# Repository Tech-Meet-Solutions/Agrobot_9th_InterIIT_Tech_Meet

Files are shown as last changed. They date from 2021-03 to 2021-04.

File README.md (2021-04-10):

# Agrobot Design Innovation Challenge
## Rural Technology Action Group - North East (RuTAG-NE)

This repository is a collection of files including simulations, CAD models and documentation created by the IIT Bombay contingent for the Agrobot Design Innovation Challenge by RuTAG-NE for Inter-IIT Tech Meet 9.0 by IIT Guwahati.  

## Abstract  

North-East India has several favorable features for agriculture from fertile land to abundant water resources (high and dependable rainfall). It has a potential to utilize these optimally for agricultural productivity. We propose to design a cost-effective, eco-friendly, and easily operable agricultural robot to convert the incumbent but less effective subsistence farming into efficient mechanized farming by harnessing appropriate niche potentials of marginal mountain land. Our Agrobot deals in particular with effective braking in hilly terrains, transplantation of plants, seed metering, and weed removal, and we do suggest extra features that may supplement the needs of the farmer on an as-needed basis.  

## The Team  

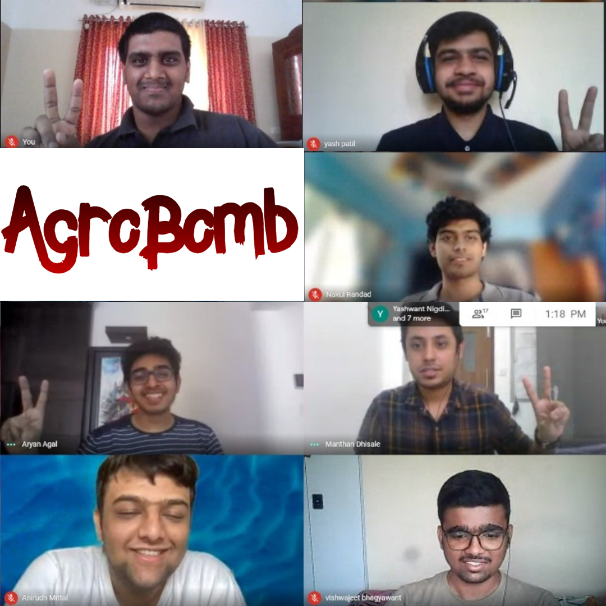
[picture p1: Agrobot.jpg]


But we miss Kaustubh and Jatin in the pic... Anirudh Mittal is the General Secretary - Technical Affairs, IIT Bombay (2020-21), and Aryan Agal and Manthan Dhisale are the Contingent Leaders of the IIT Bombay Contingent, Bombay76, for the 9th Inter-IIT Tech Meet.  

## Team Members

- [Nakul Randad](https://nakulrandad.github.io) *(Team Lead)* 
- [Aaron John Sabu](https://sites.google.com/view/aaronjs/)  
- [Vishwajeet Bhagyawant](https://vishwajeetiitb.github.io/) *(Team Lead)* 
- [Jatin Prashath](https://www.linkedin.com/in/jatin-prasath-399546183/)  
- [Yash Patil](https://www.linkedin.com/in/yash-patil-675863194/)  
- [Kaustubh Patil](https://www.linkedin.com/in/kaustubh-patil-04/)  

### The contingent won Bronze Medal 🥉 in the RuTAG-NE Agrobot Design Innovation Challenge.

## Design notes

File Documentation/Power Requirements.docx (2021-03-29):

Actuator Description | Number of Pieces | Unit Power | Total Power
Locomotion Motor | 4 pieces | 1000 W | 4000 W
High-Power Stepper Motor | 4 pieces | 100 W | 400 W
Stepper Motor (NEMA23) | 1 piece | 9 W | 9 W
300 mm stroke pneumatic cylinder | 1 piece | 50 W | 50 W
50 mm stroke pneumatic cylinder | 2 pieces | 20 W | 40 W
Solenoid valves | 3 pieces | 15 W | 45 W
Servo motor | 1 piece | 7.5 W | 7.5 W
Stepper motor (NEMA23) | 2 pieces | 9 W | 18 W
Gimbal Stepper Motors (NEMA17) | 2 pieces | 15 W | 30 W
Powder gate servo motor | 1 piece | 7.5 W | 7.5 W
DC Motor | 1 piece | 35 W | 35 W

Total Power Requirement = 4000+400+9+50+40+45+7.5+18+30+7.5+35 = 4602 W

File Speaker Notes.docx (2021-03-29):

# Speaker Notes

# (RuTAG) NORTH EAST's AGROBOT DESIGN INNOVATION CHALLENGE

### 2021-03-28

AARON (Backup: NAKUL)

# Slide 01

- Hi everyone. Here’s a quick look at our design for the agrobot.

# Slide 03

- Being modular in design, our robot can carry out tasks such as sapling transplantation, weed removal, and seed metering not just on planes but also in hilly terrains.

# Slide 07

- The agrobot uses a 4-wheel drive with individual steering instead of a differential turning mechanism for more traction and less slippage on loose soil.
- Moreover, the steering motors can align the wheels in a staggered manner for braking.
- The robot features an adjustable chassis to alter wheel separation.

# Slide 13 (Video)

- The proposed bot can sow seeds of irregular sizes at an adjustable rate with uniform penetration into the soil.
- Given the physical characteristics of the seed, we calculate the seed shape index to decide the appropriate rotating disc for the metering mechanism.
- The plastic parts in the mechanism also reduce the possibility of damage to seeds.

# Slide 19 (Video)

- Here are the main features of the transplantation module:
  - Uniform plantation is incorporated, resulting in higher yield.
  - The bot can be refilled directly with a nursery seedling tray in which saplings have been grown.
  - The bot can also plant seedlings according to specified depths as required by the plant.

# Slide 23 (Mechanical vs Chemical, Traditional vs Precision)

- When we think of weeding, we first think of a mechanical weed removal technique.
- But successful mechanical weeding requires the complete uprootal and disposal of weeds, and hence extremely precise and complex mechanisms.
- Chemical weeding, being much faster, is also more scalable in medium-scale and large-scale farms.
- These reasons demand the need for using weedicides.
- We particularly promote precision spraying for increasing the efficiency of spraying and hence decreasing the farming costs.

# Slide 27

- The extra features of the agrobot include the use of renewable power sources, terrain mapping and the identification of water stagnation zones.
- Moreover, a cooperative ownership model can be adopted and custom hiring centres developed for ease of access to the agrobot.

# Q&A

INNOVATIONS

- We have an adjustable chassis and independent steering
- We have developed sowing capability for irregular seeds using controlled metering
- The design implements a full-fledged sapling transplantation mechanism for the given size class of robots
- We have implemented chemical weeding due to the cons of mechanical weed removal. The farmer may also use organic weedicides to reduce the injection of chemicals into the food chain.

DIMENSIONS OF ROBOT

- Dimension: 0.8m x 0.8m x 0.7m
- Weight: 55kg
- Speed: RPM is high. Can reach >2m/s
- Optimum speed considering our use case: 0.5m/s
- Ground clearance: 20 cm
- Battery: 2*22Ah, 22.2V, 2hr endurance
- Steering motor torque: 42 kg-cm

CONTACT OF CROP WITH WEEDICIDE

- This also reduces the contact of the crop with the weedicide, even when the farmer chooses to use inorganic chemicals.

# Speaker Notes

# (RuTAG) NORTH EAST's AGROBOT DESIGN INNOVATION CHALLENGE

### 2021-03-27

NAKUL

A very good afternoon to one and all present here

# Slide 1

Let's start with some food for thought! What if our farmers do not need to carry out farming tasks in scorching sun or some extreme weather? Can't we use our so-called technological advances to help them with these seemingly trivial tasks.

Here we present our concept for The AgroBot to cater their needs.

Firstly let's see the major hurdles in farming related activities.

# Slide 2

Labor shortage, smaller land holdings, inferior farm yield and lower tendency to adopt new mechanisms are few of the many problems that AgroBot can help eliminate.

# Slide 3

With a modular design our robot can carry out tasks like sapling transplantation, weed removal, seed metering not only on planes but in hilly areas as well.

I call upon Yash to dive into the mechanisms in detail.

YASH

# Slide 4

So coming to slippage prevention system

# Slide 5

As our main target was to mechanise agriculture in hilly terrain , our bot has 3 salient features structurally modified wheels

manoeuvring and alignment on these slopes, the

4-wheel drive design with high ground clearance

The wheels consist of rigid-rim, wire-mesh tires that are connected to their axles by spokes. Metal cleats are also mounted on the tire to ensure better traction in the loose soil.

Center of gravity is tried to kept as low as possible

# Slide 6

Components of different

Adjustable rod : Adjust track and wheelbase

High ground clearance and low COG

# Slide 7

2 systems incorporated to avoid slippage

Control system and Mechanical system

4 wheel drive as the soil is loose to avoid slippage and it will give better traction

On high gradient surface the staggered alignment of wheel help in maintaining the position of the bot

NAKUL

# Slide 8

Now coming to the seed metering mechanism, this is an important task as we need to monitor the number of seeds soon at a location without wasting them.

# Slide 9

The design proposed by us can sow seeds of irregular varied sizes at a controllable rate with uniform penetration in the soil.

# Slide 10

The components of the mechanism are shown here. This includes a seed storage box, a continuously rotating disc with slots for seeds, mechanism to put the seeds appropriately in the slots and finally seed sowing pipe.

# Slide 11

Given the dimensions and phy characteristics of the seed we calculate a seed shape index which helps us decide the rotating disc to be used for the metering mechanism.

Of course these discs are easily replaceable.

The plastic parts in the mechanism reduce the chances of damage to the seeds.

# Slide 12

The mechanism as earlier seen in the picture follows this routine.

1) Seeds are first dumped into the hopper and later put into appropriate slots in the rotating disc which fall into delivery pipe

3) and finally the seeds are sown at uniform penetration through a pneumatics actuated delivery pipe.

# Slide 13

Lets watch a quick simulation of the working of mechanism

# Slide 14

With the angular velocity of rotating disc, forward velocity of robot and the state of pneumatics actuated delivery pipe we can control the number of seeds to be sown at what location.

This shows all the boxes for seed metering mechanism are thus checked.

# YASH

# Slide 15

Uniform plantation: equal spacing between plants ...gives higher yield

Refill the bot : Farmer can directly add the sapling trey from nursery into the bot

Plantation to required depth; as every plant requires different depth for growing optimally

# Slide 16

Seedling gripper : Mechanically holds the sapling and drops it into the seedling planter mechanism

The tray is moved through the motors as a conveyer belt

# Slide 17

The next modular accessory is transplantation,

The main features are

Firstly, the uniform plantation - which results in higher yield

Second, you can refill the bot directly with your nursery seedling tray in which you have grown your sampling

And last but not least it will plant the seedling according to the required depth

Coming to the mechanical part

It comprises two mechanisms

1st is seedling gripper & 2nd is a seedling planter

# Slide 18

The mechanism is way simpler,

It contains the gripper which grabs the seedling from the tray and drops it in the planter,

And at the same time another mechanism for moving the tray along the row when the seedling is removed from the hole, and when rows are finished the tray is moved down with the help of another mechanism

AARON

# Slide 20

- As we all know, weeds are a scourge for farmers.
- They reduce crop yield and even poison the soil.
- Weed removal is an essential requirement for any farmer and hence finds its way into our design.

Slide 21

- Our weed removal mechanism features the following characteristics:
  - Organic weedicides that nourish the soil can be loaded into the mechanism.
  - The farmer may spray both liquid and powder in a very precise manner.
  - This mechanism can also be used to sprinkle fertilizers to the plants.
  - And the nozzle of the mechanism is customizable to permit widespread spraying as well as focused spraying.
- Here are some details of our mechanism:
  - The 2-axis gimbal permits spraying throughout the region around the bot.
  - An atomizer is implemented as a very thin tube for spraying liquid weedicide.
  - The junction permits the mixing of solid and liquid with compressed air for precise and focused spraying.
  - An agitator can also be used to maintain smooth flow of powdered weedicide without clogging inside the pipes. We’ll also see more of this later.

Slide 22

- So what’s inside the junction?
  - The upper hole, that’s the smallest hole, is the atomizer through which the liquid weedicide comes out
  - The large middle hole is the input point for compressed air
  - And the hole in the bottom is where the powder comes in.
- For more control, there may also be a gate mechanism for the solid weedicide input and a valve for preventing the flow of compressed air into the liquid weedicide tube.

Slide 23

- The first thought that comes to our minds when we think of weeding is a mechanical weed removal technique. So, why haven’t we suggested that instead of weedicides?
- The complete uprootal, segregation, and disposal of weed are required for successful mechanical weed removal.
- This calls for an extremely precise mechanical arm mechanism that would be complex to implement and would put a dent in the wallet of the farmer. It would also be difficult to maintain in the rough conditions of a farm.
- Moreover, mechanical weed removal may even cause damage to crop roots.
- Finally, mechanical weeding is much slower in comparison to chemical weeding, which makes the latter much more scalable in medium-scale and large-scale farms.
- These reasons demand the need for using weedicides.
- But why not traditional weed removal? Why specifically use precision spraying?
- In terms of weedicide volume, precision spraying is 95% more efficient than indiscriminately spraying weedicides since it sprays only in areas that are detected to contain weed.
- While this saves a lot of weedicide and reduces costs for the farmer, it also puts smaller amounts of chemicals in the food chain even with inorganic weedicides, hence improving the quality of the crop.
- Finally, our weed removal mechanism may use computer vision to detect the location of weeds to prevent indiscriminate weeding which may lead to the removal of crops as well.

Slide 24

- The agitator is a basic mechanism that causes vibrations on the pipes.
- The mechanism works due to the unbalanced force that arises due to the unbalanced mass that is the semi-circular mass that is rotated using the DC motor.
- The agitator is placed midway between the gimbal mechanism and powder tank for optimal performance.

# Slide 25

AARON: So, what’s more? Let’s hear from Kaustubh and Nakul.

KAUSTUBH: Title

# Slide 26

Architecture: The DC battery powers the microcontroller which provides outputs to the motor driver and based on the inputs from the sensors. A solar module can be integrated for recharging the batteries.

# Slide 27

Extra features are

-> Renewable source of power: Hilly regions have high solar irradiation and a 200W solar panel mounted on the roof of the robot is enough to charge two batteries.
Which is utilization of Solar irradiation

-> Gyroscope ground level alert: Using the gyroscope of a smartphone integrated with a bot, the bot alerts farmers where water stagnation can occur .
Which can map the terrain and help identify water stagnation zones with soil moisture sensors

-> All of this can be integrated into a smartphone application for ease of use.

Smartphone integration: Once a farmer connects his smartphone, the bot becomes aware of farm layout, crop type and farm activities to be carried from data in the smartphone. The ambient light sensor , gravity sensor , gyroscope, compass, camera, flash from a smartphone are available for bot to use.

3D printable parts: Several parts of the mechanism plastic made to prevent damage to seeds and saplings and can be modified as per required customisation.

-> Disease assessment on crops and light traps : The light trap mounted on the bot traps insects as it moves through the farm at night. The continuous surveillance using a smartphone camera and a computer vision algorithm keep track of yellowing and rolling of leaves and alert farmers with photos and crop location. Manual steering option: A handlebar at the back of bot gives full steering control with motor locomotion

# Slide 28

Cost issues are answered by implementing cooperative ownership model and custom hiring approach

Energy issues are answered by using renewable energy power.

Innovations can help reducing fixed and variable costs.

# Slide 29

The role of Agrobot in the rural sustainability triangle is explained in terms of economic, socio-cultural and environmental aspects.

Socio-cultural

Rural Social Condition: Due to migration of men to cities, women have to lead farm activities. The mahila mandals, self -help groups (SHGs) in several hilly states have the potential for women in the development of cooperative ownership model and custom hiring centres in hilly areas.

Food Quality:Low use of agro-chemicals indicates considerable potential for ‘organic’ agriculture.

Farmer Safety: high risk of work-related injuries, lung disease, noise-induced hearing loss, skin diseases, as well as certain cancers related to chemical use and prolonged sun exposure

Youth skills: micro enterprises development

Economic

Farmer Income: labour decrease, seed and other input cost,

Sustainable food products: diversify into more lucrative high value crops.

Food supply: subsistence farming into viable farming

ENVIRONMENT:

Soil/ water : New technologies prevent land loss to erosion, water pollution and enhances carbon sequestration.

Biodiversity: Local species of food products (species, fruits, vegetables_ are conserved.

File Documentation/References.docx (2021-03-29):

# References

1. Potential Bioherbicides: Indian Perspectives | SpringerLink (https://link.springer.com/chapter/10.1007/978-81-322-1683-4_15)
2. Distinguish between selective and non-selective herbicides and give an example of each. | Forage Information System | Oregon State University (https://forages.oregonstate.edu/nfgc/eo/onlineforagecurriculum/instructormaterials/availabletopics/weeds/herbicides)
3. Mechanical Weed Control - ScienceDirect (https://www.sciencedirect.com/science/article/pii/B9780128098813000085)
4. Bio-herbicides For Sustainable And Eco-friendly Weed Control: A Review. (journalijar.com) (http://www.journalijar.com/article/26030/bio-herbicides-for-sustainable-and-eco-friendly-weed-control:-a-review/)
5. Limitations of Existing Weed Control Practices Necessitate Development of Alternative Techniques Based on Biological Approaches - ScienceDirect (https://www.sciencedirect.com/science/article/pii/S0065211317300858)
6. Farming Bot: Precision Agriculture System in Limited Land Based On Computer Numerical Control (CNC) (https://iopscience.iop.org/article/10.1088/1755-1315/411/1/012059/pdf)
7. Different Types of Agricultural Robots | RIA Robotics Blog (https://www.robotics.org/blog-article.cfm/Robotics-in-Agriculture-Types-and-Applications/74)
8. Highlights of Himalyan farming book (https://docs.google.com/document/d/1mqfsVbrNtr3RH_c4kIhuxth0uB1VbZMfozKEREzDgDA/edit?usp=sharing)
9. Rowbot (https://rowbot.com)
10. About – Harvest Croo (https://harvestcroo.com/about/)
11. CAD
  a. Motors: https://grabcad.com/library/1020zxf-36v-500w-dc-motor-1
  b. Seedling: https://grabcad.com/library/seed-starter-tray-insert-1
12. Products
  a. Motors: https://robu.in/product/my1020-48v-1000w-electric-go-kart-brushed-dc-motor-with-foot/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

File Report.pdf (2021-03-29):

# Ag r o B o t De s i g n I n n o v a ti o n C h a l l e n g e

## INTER I IT TECH MEET '21

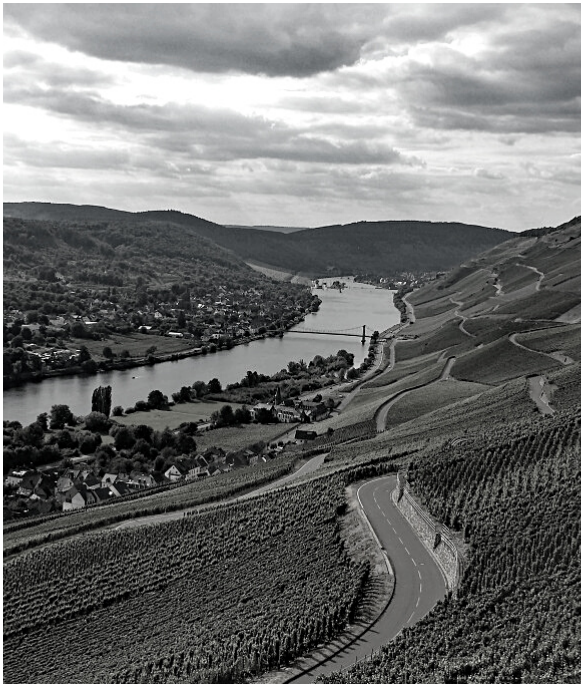
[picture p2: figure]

## Introduction to Solutions

### Literature review and survey

The North-Eastern regions of India have several comparative features like fertile land, abundant water resources, high and dependable rainfall (annual rainfall about 2000 mm), and an agriculture-friendly climate. Yet, it has failed to convert its strengths optimally into growth opportunities in agricultural productivity (Barah, 2006).
We conducted an online survey and telephonic interview to understand the hill conditions, resources available, and people’s socio-cultural setting. The analysis of responses from 28 respondents about farm activities that require mechanization is as follows:

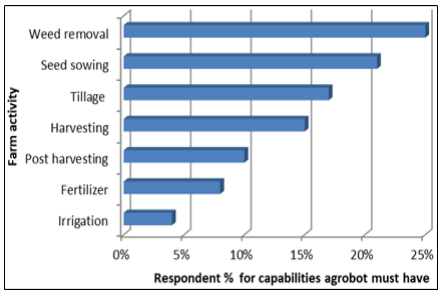
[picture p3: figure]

Fig.1: Survey on AgroBot capabilities

We realized that a major portion of the land in this region has a slope of more than 15°, undulating topography, inaccessible terrain, fragility in moisture stress, and also poor soil conditions. Moreover, socio-economic constraints exist, such as small holdings, poor productivity, production management, labour shortages, poor marketing, and lack of entrepreneurship. The objective was to design a cost-effective, eco-friendly, easily operable AgroBot to convert non-viable subsistence farming into viable farming through harnessing appropriate niche potentials of marginal mountain land.

### Mechanized farming in hilly terrain

Rationale for mechanism
Hilly farming terrains in the North-Eastern regions of India have slope gradients ranging from 2° to 27° (Prokop & Poreba, 2012). The accuracy of position calculated through odometry is affected by slippage between the ground and the wheel or track. When travelling on a loose slope, the localization accuracy of the odometry decreases remarkably due to slippage. To improve its accuracy in such environments, terra-mechanics focuses on estimating the interaction between a vehicle and the ground with visual odometry.

Manoeuvring and alignment on these slopes

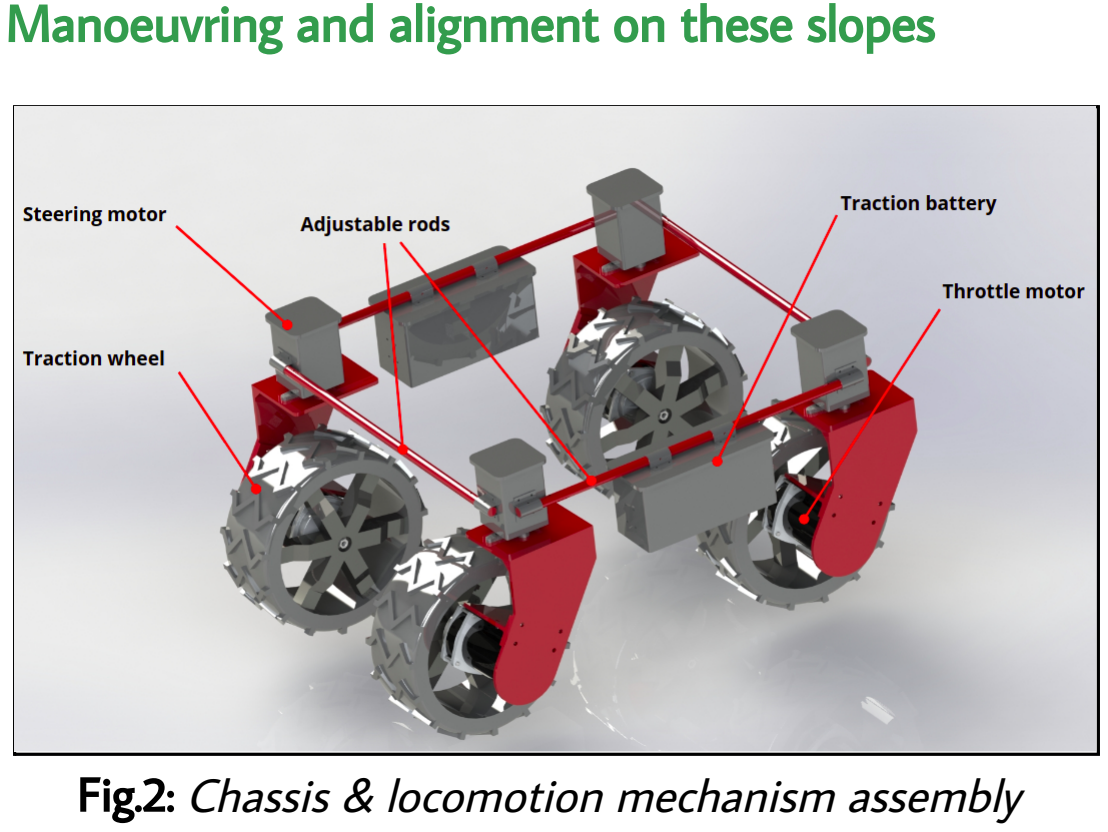
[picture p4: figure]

Fig.2: Chassis & locomotion mechanism assembly

Along with introducing a slip model to the kinematics (control), we also have mechanically modified wheels. A differential turning mechanism is not a preferred way for steering in these environments of low wheel traction. For manoeuvring and alignment on these slopes, the 4-wheel drive design of our robot coupled with each wheel’s independent steering ability serves the purpose. With these capabilities, the vehicle wheels can be aligned in a staggered fashion (see Fig.2) to reduce slippage drastically. The low centre of gravity was aimed to get a stable design that includes mounting battery pods (high-density components) as low as possible.

### A metering mechanism for irregular seeds

Rationale for mechanism
Delays in planting due to labour shortages and rain cause the rotting of rhizomes. Mechanized planting can help overcome labour shortages, improve operational timeliness, and reduce cost, drudgery, and yield losses. The seed rhizome’s shape is irregular and could not be correlated to any standard shape. However, the variability in shape is expressed as ‘Shape Index’ (I

s). The
shape index of the seed rhizome is calculated by the following expression (ISO, 1983):

I

s = [L

2
/ (W · T)] · 100
where L, W, and T (all in mm) are the length, width, and thickness of the seed respectively. Metering mechanisms with three interchangeable disks with cell sizes of diameter 80mm, 30mm, and 10 mm are provided to accommodate different seed sizes. To get the dimension of the seed metering mechanism, the mean length, width, thickness, weight, and shape of seed rhizome along with the standard deviation and coefficient of variation were measured for over 30 rhizome seeds with

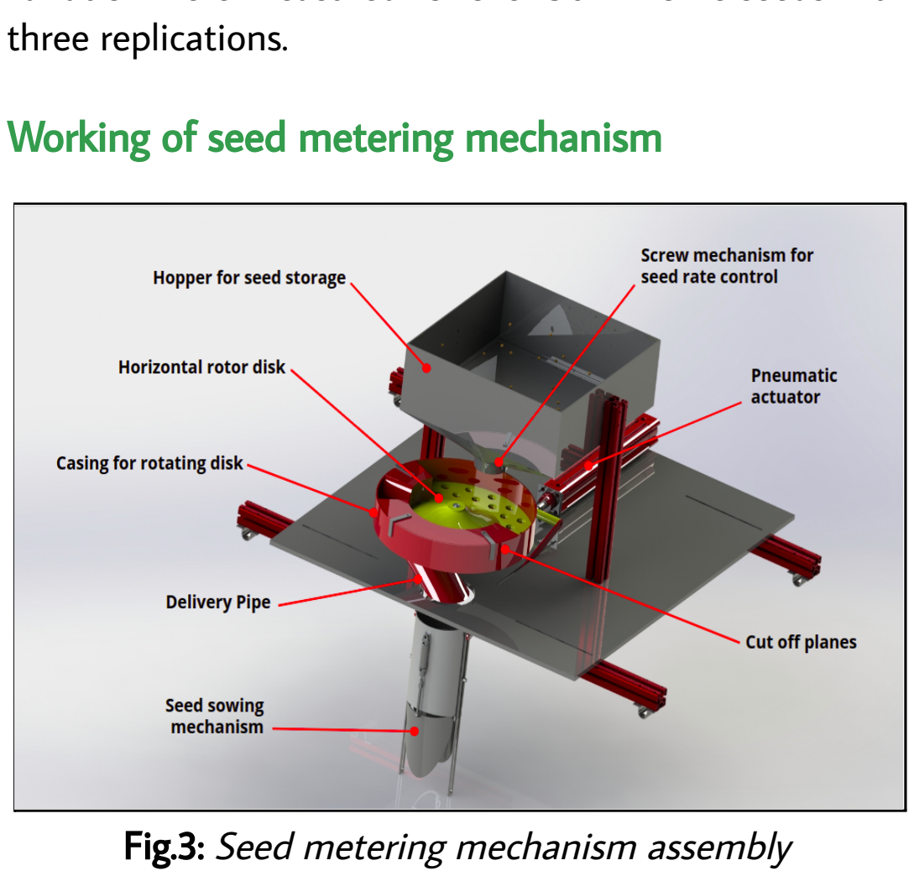
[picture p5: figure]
three replications.; Working of seed metering mechanism; Fig.3: Seed metering mechanism assembly

Seeds are dumped in the hopper from the top. At the bottom of the hopper, a screw adjustment mechanism controls seed rate falling on the horizontal disk rotor. Cut-off plates over the disk ensure that a specified seed amount fills each cell. As each cell approaches the bottom chute in the casing, the seed rhizomes drop in the delivery tube. Calibration of the seed metering mechanism (rpm of the horizontal disc) is calculated based on bot forward speed, seedling spacing, no. of cells, and disc radius. The rotor disk rotation speed ensures seed dropping at the correct spacing between plant to plant. The delivery tube drops seeds in pits created by flap-type planters at required soil penetration. Two flappers at the back of the AgroBot cover the seed with soil and compact the soil around it to enhance germination and emergence. Horizontal disc cell type, the metering mechanism has high cell fill accuracy from past testing and is reliable.

### Transplantation mechanism

Rationale for mechanism
Rhizomes seeds are stored in soil pits in a dry and shaded place between cropping seasons. In this method, around 25-30% of rhizomes rot in the pit itself, and about 10-15% of rhizomes sprout in the hole and are rendered useless for sowing. Transplantation can prevent these losses.
Working of Transplantation mechanism
The transplantation mechanism is inspired by flap-type planters. We have automated a flap-type planter using three pneumatic cylinders, a cylinder for pushing the flaps/blades into the ground, and another two cylinders to open and close the flaps.

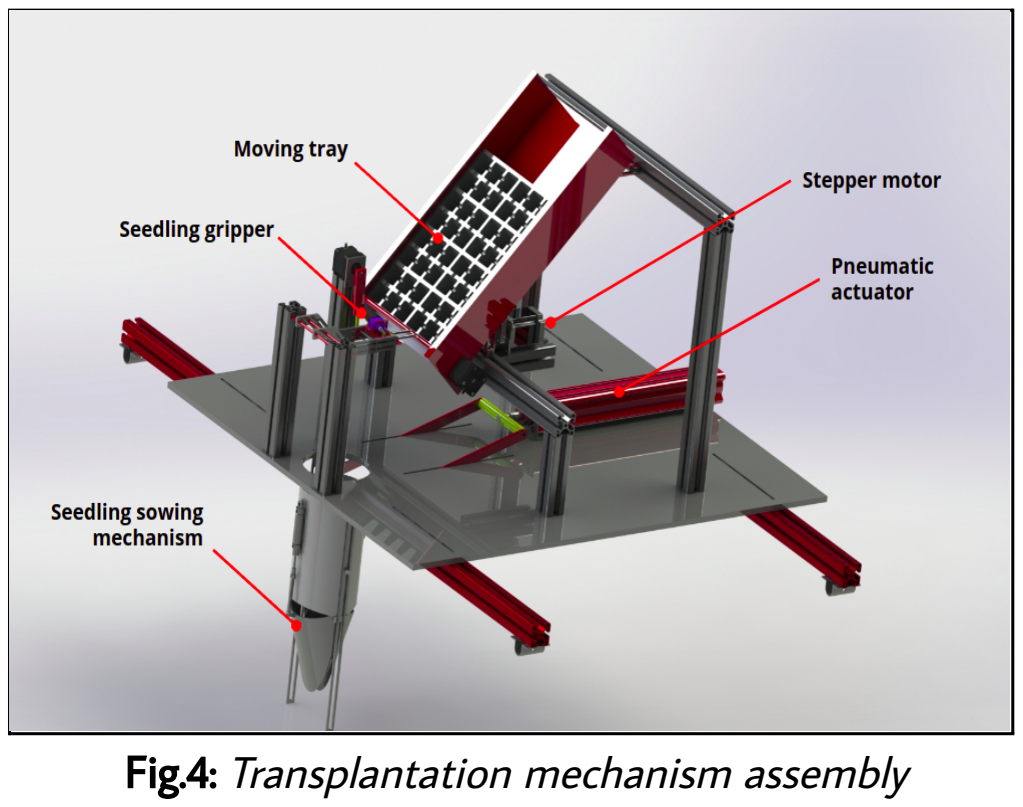
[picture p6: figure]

Fig.4: Transplantation mechanism assembly

The conveyor mechanism is implemented for the automatic supply of saplings to the planter. We have used a tray that will work like a conveyor belt and contain saplings for plantation. The tray will be mounted on a system with 2 DoFs, due to which the tray will be able to move in the azimuthal plane. A gripping / clipping mechanism is also added to drop saplings into the planter. Three motors are being used; 1 servo (for gripping mechanism) and 2 NEMA 23 motors for operating the conveyor tray.

### Weed removal mechanism

Rationale for mechanism
There are two options available for weed removal: mechanical and chemical. We have opted for organic herbicides weed removal for the following reasons: Mechanical weed removal requires the complete uprootal of weeds and their disposition away from the field. If this is not achieved, they will grow back in no time, making the process ineffective. The mechanical weed removal process can trigger soil erosion on steep slopes. Studies on steep slopes have indicated the soil loss of order 40.9 tonnes/ha.

Weeds grown within crop rows and closer to crop plants escape the mechanical remover and can also damage roots. Weeds grown within crop rows incur much higher losses. Furthermore, weed removal products with biological control agents (BCAs) act as sources of nutrition for the soil. They help provide agriculture with effective tools for abundant crop production while minimizing impacts on health and the environment.

Working with herbicide and powder application

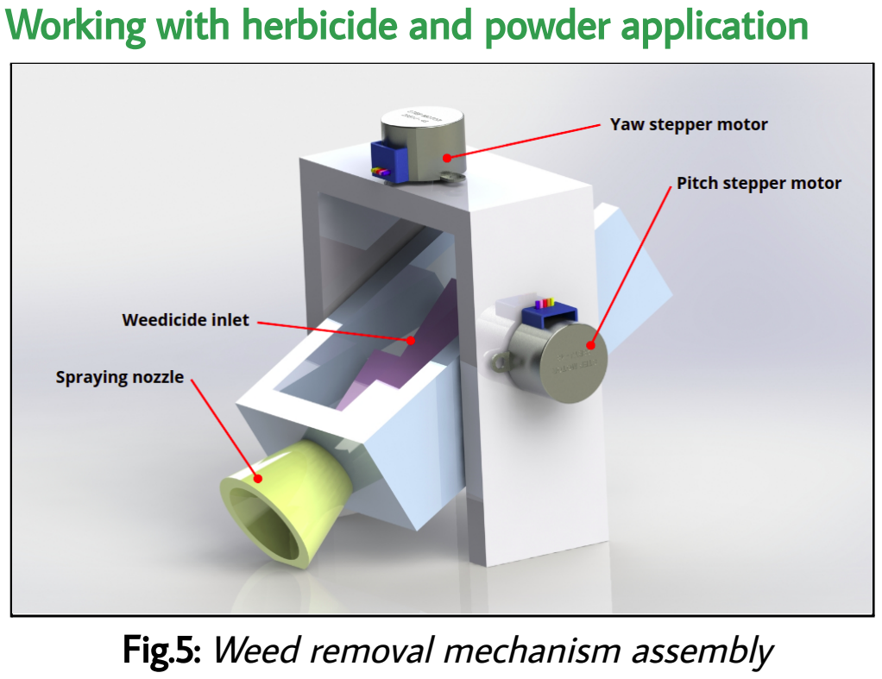
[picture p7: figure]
Fig.5: Weed removal mechanism assembly

Insect-pest control through ITK (Indigenous Technical Knowledge) involves the sprinkling of ash and powdered farmyard manure (FYM). The proposed mechanism can spray both liquid and powdered products. Both mechanisms are operated by spraying air at high pressure through a specially designed nozzle where the air mixes with liquid or powder and then exits via a nozzle. A 2-axis gimbal controls the direction of the nozzle. This allows us to control the region where the product is sprayed and increase the efficiency of spraying the organic product by reducing its wastage. The proposed mechanism can also be used for spraying fertilizers and other kinds of additives.

## Model details

### Mechanical assembly

The robot has a 4-wheel drive design which helps in generating greater torque for the movement. The wheels consist of rigid-rim, wire-mesh tires that are connected to their axles by spokes. Metal cleats are also mounted on the tire to ensure better traction in the loose soil. The seed metering mechanism, transplanting mechanism and weed removal mechanism have a rectangular platform. The platform is bolted to the base frame and the mechanism gets easily integrated. The base rod mounting points are changeable which gives the user freedom to vary the distances between wheels as per the crop/terrain requirement.

### Electronics

IMU (Inertial Measurement Unit): This sensor can help with getting the acceleration and orientation of the AgroBot. The acceleration can be used to calculate velocity and distance travelled. Orientation can further be used to map the terrain and formulate better routes for later runs. The farmer may subsequently utilize this data to plan cropping patterns.
Smartphone Camera: It is used to identify weeds, monitor surroundings, help with navigation and provide visual feedback to the remote user.
Soil moisture & temperature sensor: It is used to measure the volumetric water content of the soil. This helps to plan the farming activities better with proper data collection for each event.
Sensor Positioning: The sensors are attached to the robot’s frame with sturdy mounts, which helps avoid possible damages to the sensor. These mounts are modular, which enables the user to remove and incorporate a sensor into the robot.

### Architecture

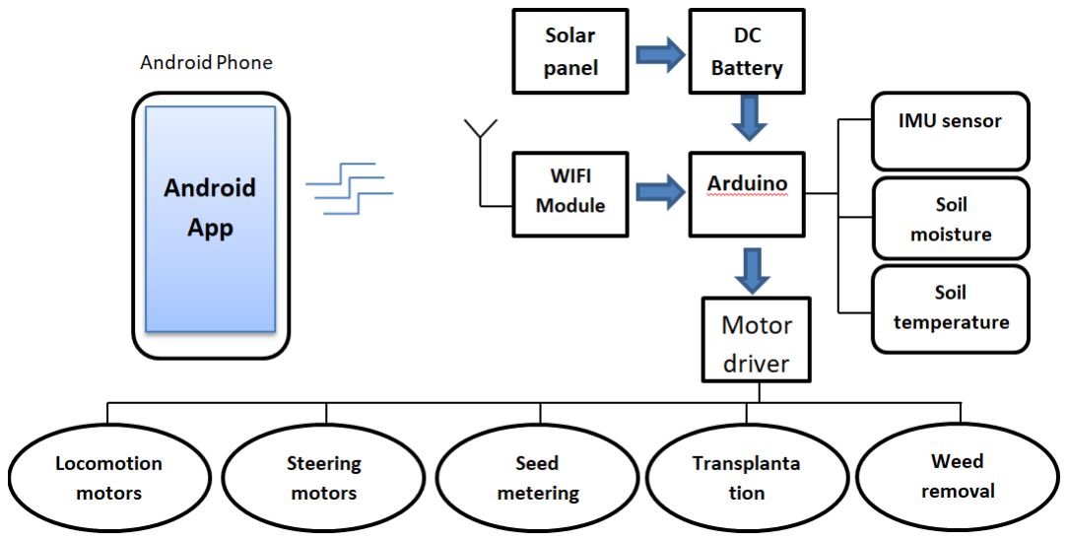
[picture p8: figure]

Fig.6: Block diagram of Agrobot

## Hardware Components & Cost Analysis

Cost for mechanized farming in hilly terrain
Sr. no. | Main component | Sub-components | Cost/pc | Qty
1 | Wire mesh tyres (with extrusions) | Rim | 1200 Rs | 4 pieces
2 | Locomotion Motor (1000 Watts): Throttle* | Fitting and wiring | 5000 Rs | 4 pieces
3 | Stepper Motor (NEMA34) 100 Watts, 42kg-cm: Steering (Link)* | Fitting and wiring | 3000 Rs | 4 pieces
4 | Batteries (22000mAh; 22.2 V) - 1 hr endurance | LiPo type | 11000 Rs | 2 pieces
5 | Solar Panel (200 W, 24 V) - optional | Controller | 5000 Rs | 1 piece

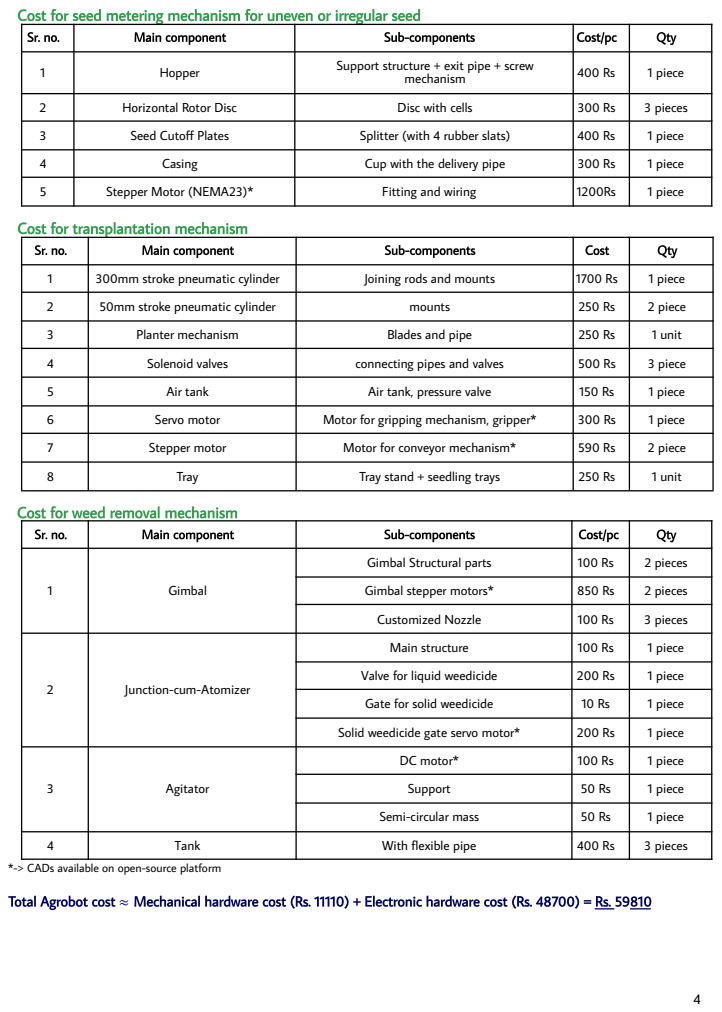
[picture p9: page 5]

Cost for seed metering mechanism for uneven or irregular seed

Sr. no. | Main component | Sub-components | Cost/pc | Qty
1 | Hopper | Support structure + exit pipe + screw mechanism | 400 Rs | 1 piece

2 | Horizontal Rotor Disc | Disc with cells | 300 Rs | 3 pieces
3 | Seed Cutoff Plates | Splitter (with 4 rubber slats) | 400 Rs | 1 piece
4 | Casing | Cup with the delivery pipe | 300 Rs | 1 piece
5 | Stepper Motor (NEMA23)* | Fitting and wiring | 1200Rs | 1 piece

Cost for transplantation mechanism

Sr. no. | Main component | Sub-components | Cost | Qty
1 | 300mm stroke pneumatic cylinder | Joining rods and mounts | 1700 Rs | 1 piece
2 | 50mm stroke pneumatic cylinder | mounts | 250 Rs | 2 piece
3 | Planter mechanism | Blades and pipe | 250 Rs | 1 unit
4 | Solenoid valves | connecting pipes and valves | 500 Rs | 3 piece
5 | Air tank | Air tank, pressure valve | 150 Rs | 1 piece
6 | Servo motor | Motor for gripping mechanism, gripper* | 300 Rs | 1 piece
7 | Stepper motor | Motor for conveyor mechanism* | 590 Rs | 2 piece
8 | Tray | Tray stand + seedling trays | 250 Rs | 1 unit

Cost for weed removal mechanism

1 | Gimbal | Gimbal Structural parts | 100 Rs | 2 pieces

Gimbal stepper motors* | 850 Rs | 2 pieces
Customized Nozzle | 100 Rs | 3 pieces

2 | Junction-cum-Atomizer | Main structure | 100 Rs | 1 piece

Valve for liquid weedicide | 200 Rs | 1 piece
Gate for solid weedicide | 10 Rs | 1 piece
Solid weedicide gate servo motor* | 200 Rs | 1 piece

3 | Agitator | DC motor* | 100 Rs | 1 piece

Support | 50 Rs | 1 piece
Semi-circular mass | 50 Rs | 1 piece

4 | Tank | With flexible pipe | 400 Rs | 3 pieces

*-> CADs available on open-source platform
Total Agrobot cost ≈ Mechanical hardware cost (Rs. 11110) + Electronic hardware cost (Rs. 48700) = Rs. 59810

## Maintenance

Transplantation mechanism
The planter mechanism has a low cost and is easy to repair. Connecting rods can be easily replaced with any metal rod (even cycle spokes temporarily). The only major components that need regular oiling and cleaning are the pneumatic cylinders and their solenoid valves. The solenoid valves may be covered with insulation to function in the rain (there are no other electrical parts). Seed metering mechanism
The seed metering device is easily detachable. It must be cleaned and oiled regularly to ensure its durability. The gap between the disk rotor and casing must be checked for any particle stuck.
Mechanised farming in hilly terrain
The wheels and base are robust and only the motors need regular oiling. The ground clearance is ~ 20 cm which reduces chances of damage to the components. Weed removal mechanism
The mechanism has very few moving parts and hence is durable. The gimbal that controls the nozzle requires maintenance but it is easily replaceable. The agitator attached to the powder carrying pipe is also replaceable by plugging although it is a moving part.

## Extra features

Renewable source of power: Hilly regions have high solar irradiation and a 200W solar panel mounted on the roof of the robot is enough to charge two batteries. Gyroscope ground level alert: Using the gyroscope of a smartphone integrated with a bot, the bot alerts farmers where water stagnation can occur.
Smartphone integration: Once a farmer connects his smartphone, the bot becomes aware of farm layout, crop type and farm activities to be carried from data in the smartphone. The ambient light sensor, gravity sensor, gyroscope, compass, camera, flash from a smartphone are available for bot to use.

3D printable parts: Several parts of the mechanism plastic made to prevent damage to seeds and saplings and can be modified as per required customisation. Disease assessment on crops and light traps : The light trap mounted on the bot traps insects as it moves through the farm at night. The continuous surveillance using a smartphone camera and a computer vision algorithm keep track of yellowing and rolling of leaves and alert farmers with photos and crop location.
Manual steering option: A handlebar at the back of bot gives full steering control with motor locomotion. Humidity and temperature sensors on bot: Regional databases of environmental conditions throughout a geographical location can be sampled by a group of bots.

## Scalability and realisation

Co-operative ownership model and custom hiring to make it scalable for small landowners
The AgriBots will be hired from custom hiring centres and farmers integrate their smartphone with the bot. Employment is generated as bots in custom hiring centers will require maintenance and technological interventions. The significant trend witnessed by the northeastern states in recent times is the change in demographic patterns i.e increased male out migration. This has led to increasing farming-related workload for women. The mahila mandals, self-help groups (SHGs) in several hilly states have the potential for women in the development of these centres in hilly areas.
Value addition for small and marginalised farmers In hilly areas, low use of agrochemicals indicates considerable potential for ‘organic’ agriculture and the AgroBot assists in the same to increase crop intensity. As drudgery reduces, farmers can devote time to microenterprise development like “farming for tourism”. With the use of AgroBots as farmers get accustomed to use of technology they can access market information and move to lucrative high-value crops from local farm produce.

## References

- Barah, B. C. (2006). Agricultural Development in North-East India Challenges and Opportunities.
- International Organisation for Standardization (ISO). (1983). Agricultural Machinery Handbook, No. 13, ISO code No. 5691 (1981), pp. 387-389.
- Prokop, P., & Poręba, G. J. (2012). Soil erosion associated with an upland farming system under population pressure in Northeast India. Land Degradation & Development, 23(4), 310-321.

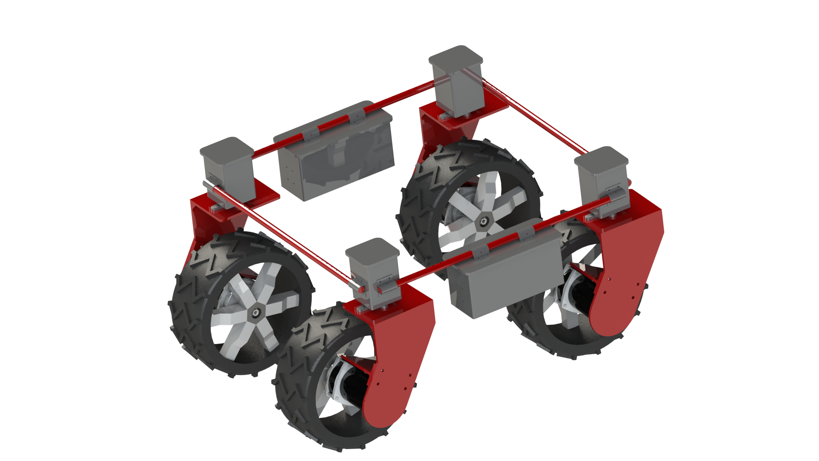
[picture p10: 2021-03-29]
Images/bot_chassis.png

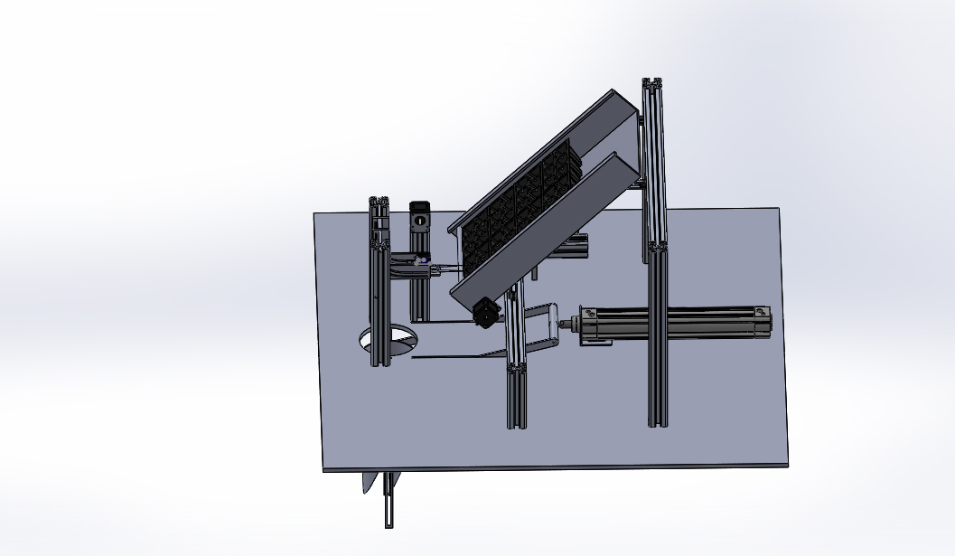
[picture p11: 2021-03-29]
CAD Files/Development/Transplantation/images/final1.JPG

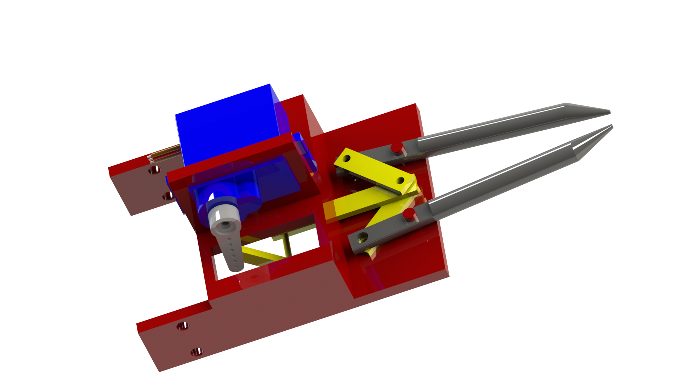
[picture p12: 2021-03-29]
Images/seedling_grabber.png

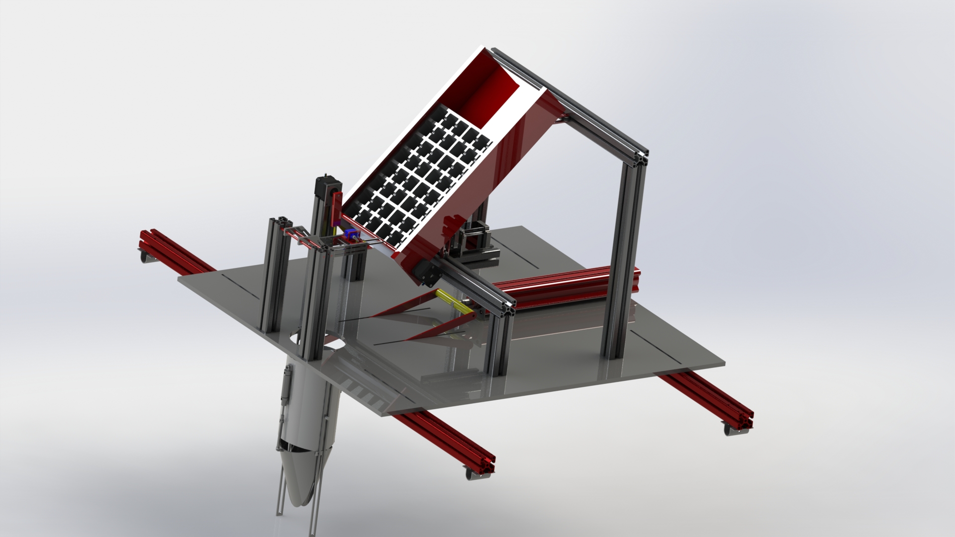
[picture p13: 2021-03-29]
CAD Files/Development/Transplantation/images/transplantation1.JPG

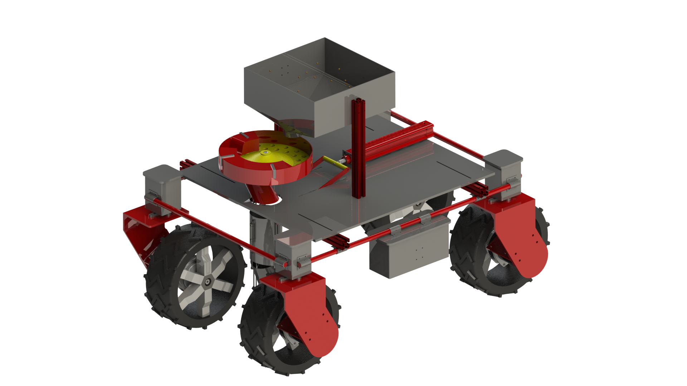
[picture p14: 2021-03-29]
Images/seed_metering_mechanism_bot2.png

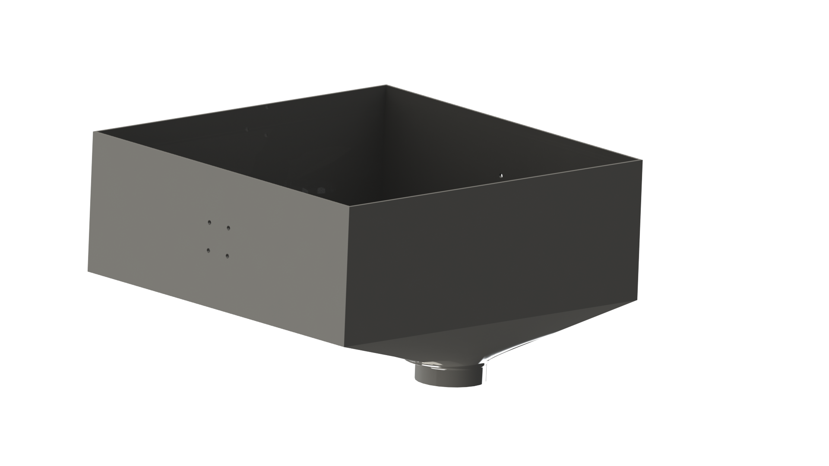
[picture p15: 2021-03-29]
Images/seed_metering_mechanism_seed_holder.png

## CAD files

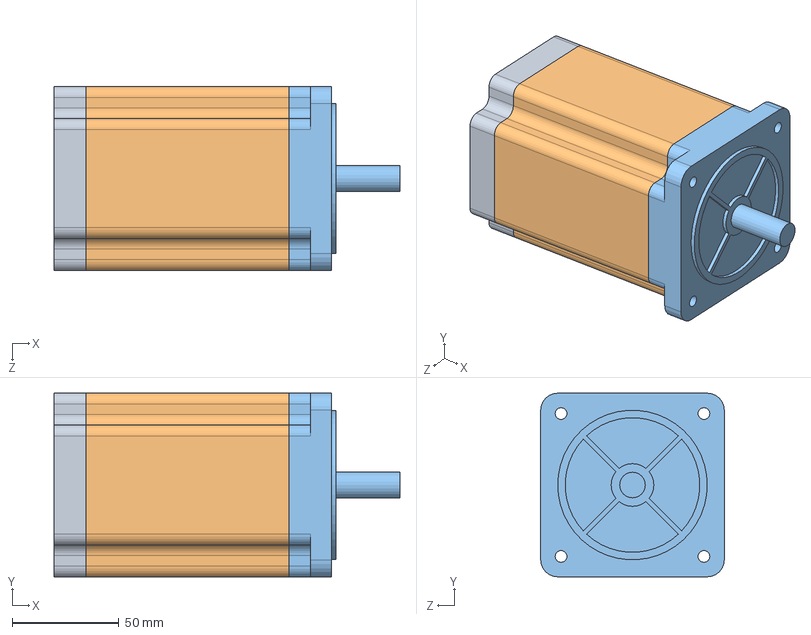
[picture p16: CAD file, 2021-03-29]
CAD Files/Development/Base/Motor/nema-34-step-motor-85kg-stepper-86-130-1.snapshot.1/steper.SLDASM
162.0 x 86.0 x 86.0 mm
back
coil
front

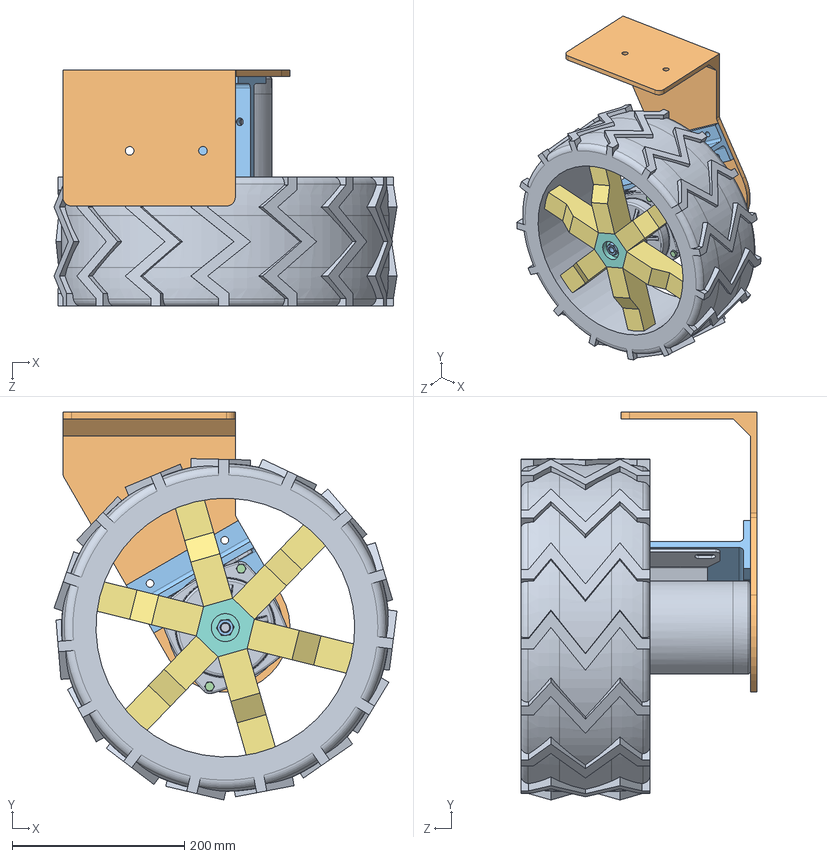
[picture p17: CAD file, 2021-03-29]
CAD Files/Development/Base/movement_assem_L.SLDASM
397.7 x 449.9 x 274.2 mm
1020ZXF-36V_500W_Motor(Domyœlna_As Machined_)
Chain wheel DIN 8192 - A 10Z 083
ISO 4034 - M12
ISO 4017 - M6 x 50 x 4
ISO 10511-M5 x 4
DIN 128 - A12
wheel_spoke x 6
wheel_hub
wheel_tire
wheel_mount_L
motor_mount

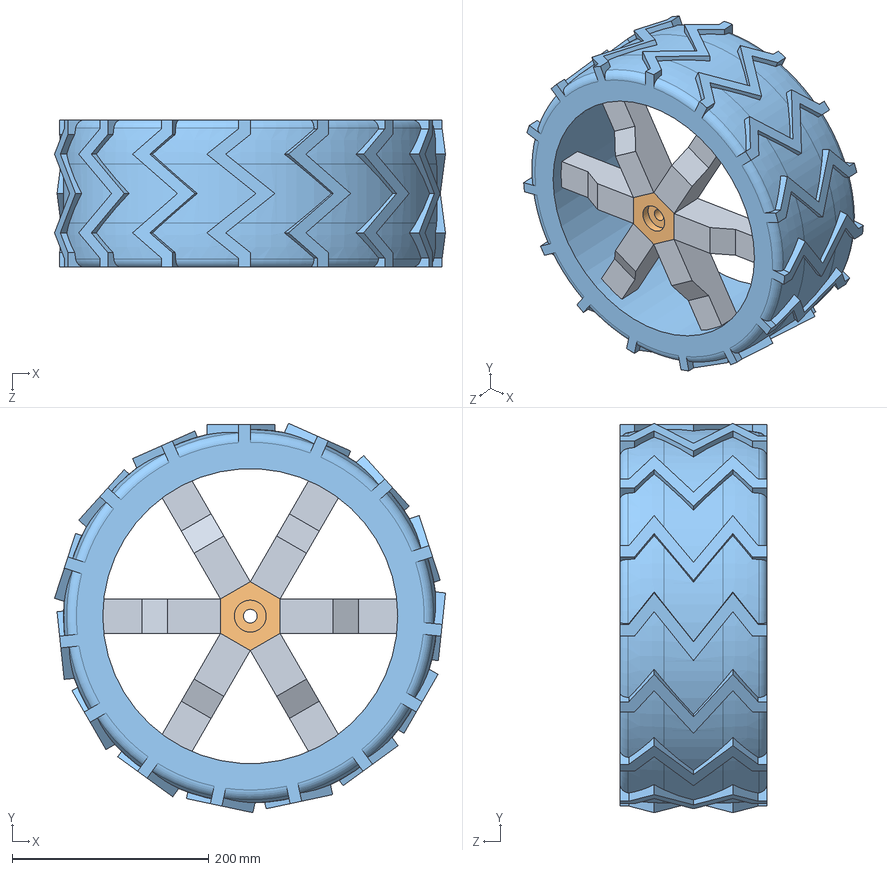
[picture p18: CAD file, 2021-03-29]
CAD Files/Development/Base/Wheels/wheel1/wheel_assem.SLDASM
397.7 x 396.1 x 150.0 mm
wheel_spoke x 6
wheel_hub
wheel_tire

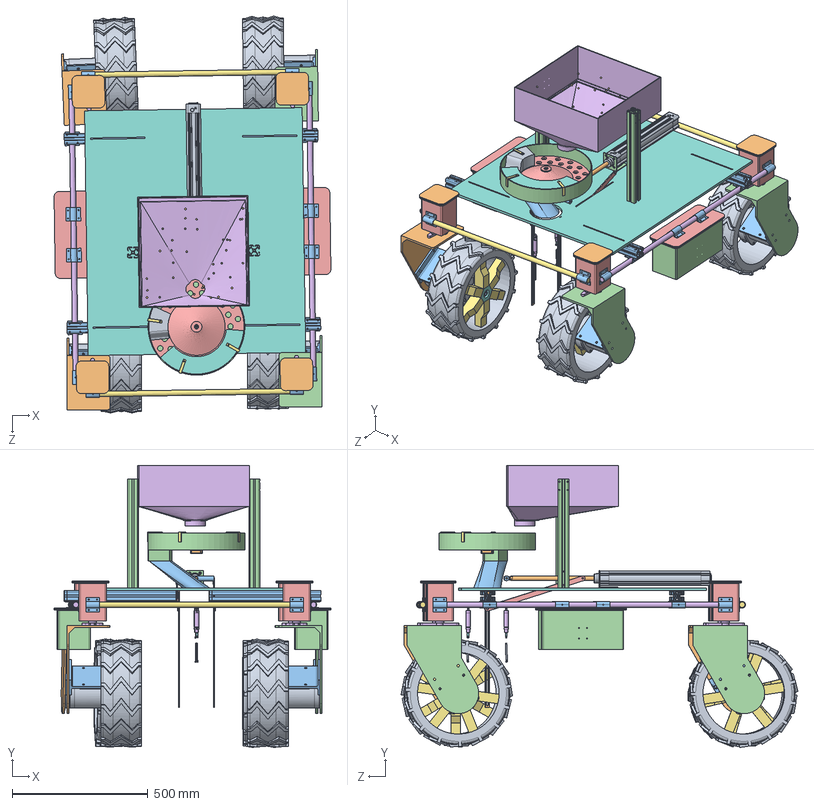
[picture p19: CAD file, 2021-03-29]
CAD Files/Development/Seedmeter/bot assembly/base.SLDASM
1018.0 x 1036.9 x 1459.7 mm
1020ZXF-36V_500W_Motor(Domyœlna_As Machined_) x 4
Chain wheel DIN 8192 - A 10Z 083 x 4
ISO 4034 - M12 x 4
ISO 4017 - M6 x 50 x 16
ISO 10511-M5 x 16
DIN 128 - A12 x 4
wheel_spoke x 24
wheel_hub x 4
wheel_tire x 4
wheel_mount_L x 2
motor_mount x 4
wheel_mount_R x 2
steering_box x 4
stepper_mount x 4
back x 4
coil x 4
front x 4
steering_box_lid x 4
C-clamp x 16
battery_box x 2
battery_box_lid x 2
length_rod x 2
width_rod x 2
test_platform
dsbc-40-300-ppva-n3_01
dsbc-40-300-ppva-n3_02
connecting_rod_1
pneumatic_1_mount
connecting_rod x 2
rod x 2
rod_end x 2
connecting_rod_2 x 2
rail x 2
flexible_rods x 4
holder
plate(10mm)
seed holder
splitter-joiner x 3
splitter-slots
hole_closure
Base
Cuerpo
Tapa
pan cross head_am x 4
Eje
instrument ball bearing_68_am x 2
socket button head cap screw_am
T5 Pulley
seed x 36
seeds_pass
funnel_stand x 2

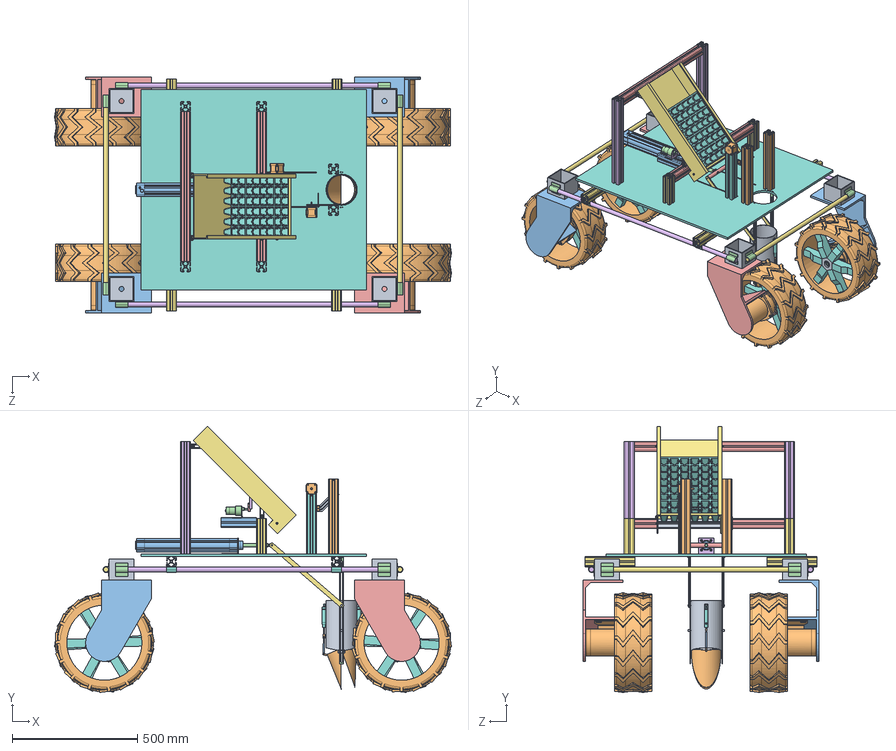
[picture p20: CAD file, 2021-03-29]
CAD Files/Development/Transplantation/bot_assembly.SLDASM
1585.3 x 1062.3 x 942.0 mm
steering_box x 4
1020ZXF-36V_500W_Motor(Domyœlna_As Machined_) x 4
Chain wheel DIN 8192 - A 10Z 083 x 4
ISO 4034 - M12 x 4
ISO 4017 - M6 x 50 x 16
ISO 10511-M5 x 16
DIN 128 - A12 x 4
wheel_spoke x 24
wheel_hub x 4
wheel_tire x 4
wheel_mount_L x 2
C-clamp x 8
wheel_mount_R x 2
length_rod x 2
width_rod x 2
test_platform
sapling_cylinder
blade x 2
dsbc-40-300-ppva-n3_01
dsbc-40-300-ppva-n3_02
connecting_rod_1
pneumatic_1_mount
connecting_rod x 2
rod x 2
rod_end x 2
connecting_rod_2 x 2
rail x 2
tray_backward_top_slider x 2
tray_backward_stands x 2
seedling_tray_holder
seed_tray_insert1
tray_mover
nema 17 x 2
cheese head screw_as
v wheel outer cover x 4
W 625-2RS1 x 8
geneva_slider
tray_forward_stands x 2
stepper_stand
nema17_clamp
path_stands x 2
geneva_motor_stand
Motor - Johnson
geneva_shaft
dc motor clamp
platform_mount x 4
mount_clamp x 4
travel_path2
slider_crank2

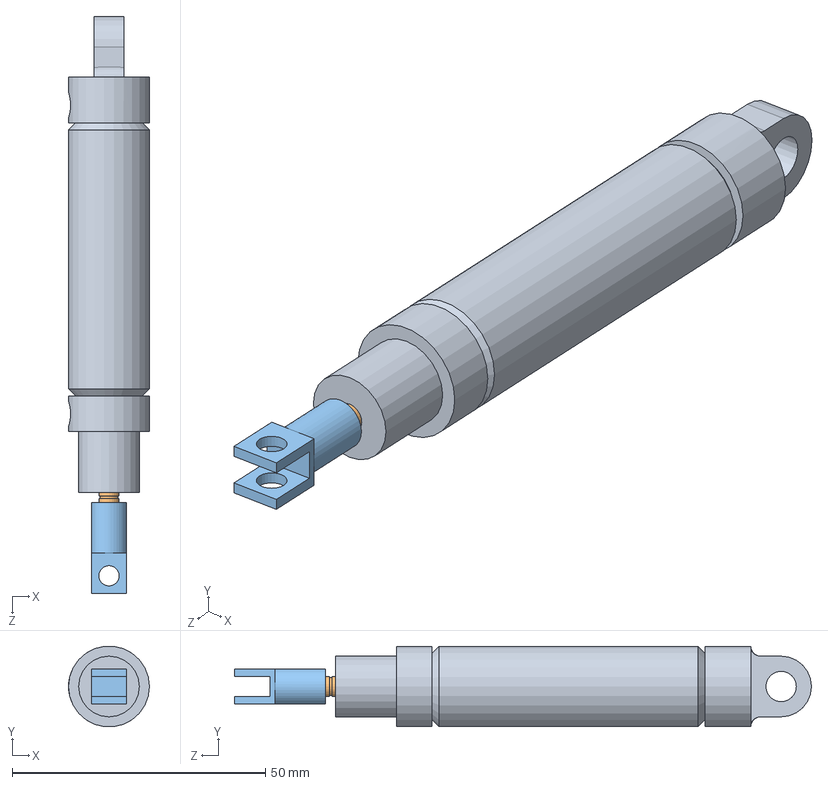
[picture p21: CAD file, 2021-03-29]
CAD Files/Development/Transplantation/planter/pneumatic_2/pneumatic_cylinder.SLDASM
16.0 x 15.9 x 114.0 mm
rod
rod_end

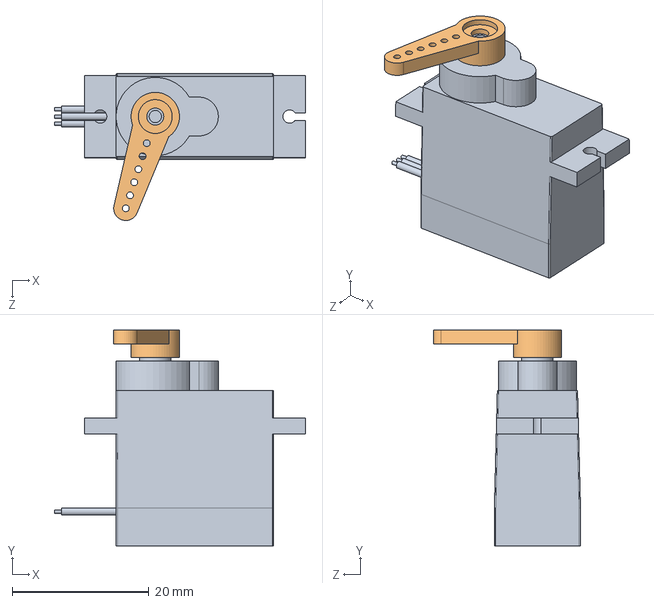
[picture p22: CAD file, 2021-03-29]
CAD Files/Development/Transplantation/seedling extractor/seedling gripper/micro-servo-9g-sg90-tower-pro-1.snapshot.2/Tower Pro 9g Micro Servo SG90.SLDASM
36.7 x 31.5 x 21.5 mm
Tower Pro 9g Micro Servo SG90
SG90 plastic Horn

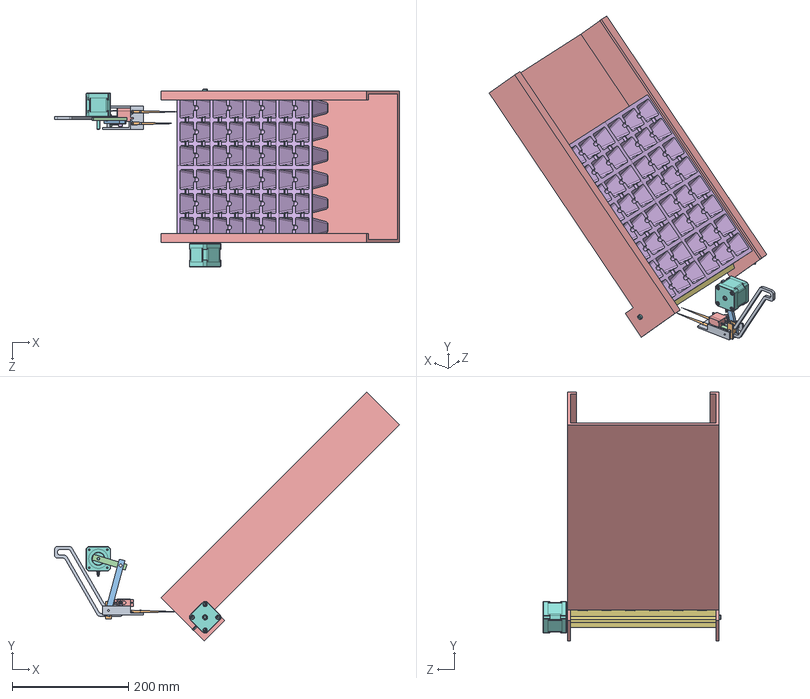
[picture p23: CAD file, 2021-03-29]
CAD Files/Development/Transplantation/seedling extractor/seedling gripper/whole.SLDASM
592.9 x 427.8 x 305.3 mm
gripper_arm_mount
gripper_arm x 2
rod x 2
rod2
Tower Pro 9g Micro Servo SG90
SG90 plastic Horn
linear_link
nema 17 x 2
travel_path
guide_slider
path_link2
path_link1
seedling_tray_holder
seed_tray_insert1
tray_mover
cheese head screw_as

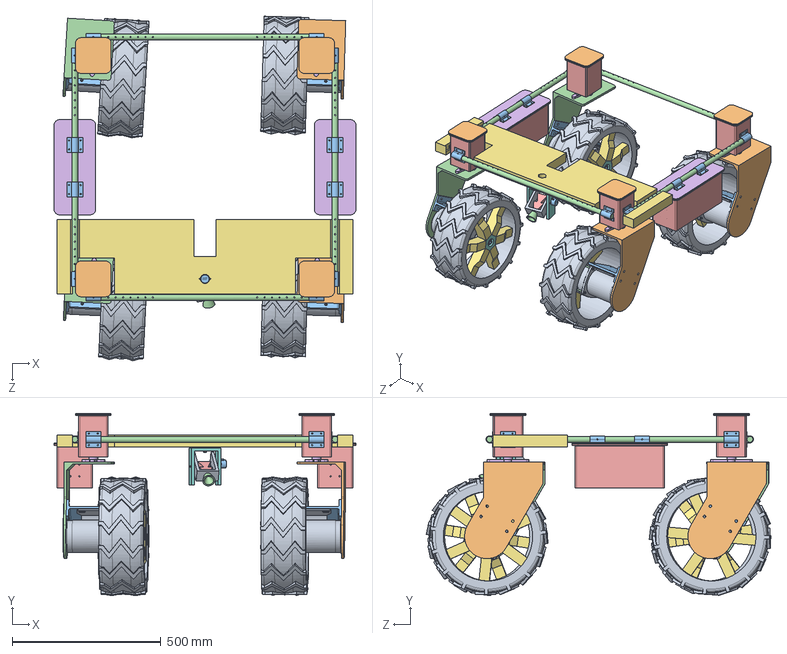
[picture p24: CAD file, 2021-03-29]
CAD Files/Development/Base/base.SLDASM
1014.0 x 612.4 x 1157.0 mm
1020ZXF-36V_500W_Motor(Domyœlna_As Machined_) x 4
Chain wheel DIN 8192 - A 10Z 083 x 4
ISO 4034 - M12 x 4
ISO 4017 - M6 x 50 x 16
ISO 10511-M5 x 16
DIN 128 - A12 x 4
wheel_spoke x 24
wheel_hub x 4
wheel_tire x 4
wheel_mount_L x 2
motor_mount x 4
wheel_mount_R x 2
steering_box x 4
stepper_mount x 4
back x 4
coil x 4
front x 4
steering_box_lid x 4
C-clamp x 12
base_rod x 4
battery_box x 2
battery_box_lid x 2
base_plate
Sprayer-OuterPiece
Sprayer-InnerPiece
Sprayer-Outer-Motor-Connector
28BYJ-48 x 2
Sprayer-Nozzle-01
Sprayer-Junction

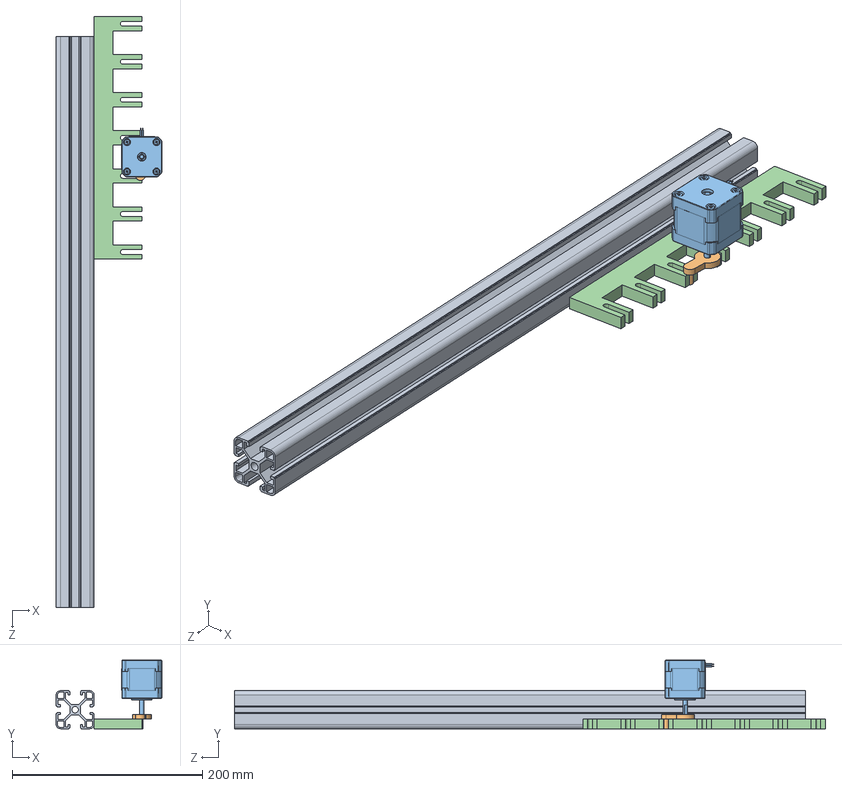
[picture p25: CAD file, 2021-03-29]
CAD Files/Development/Transplantation/geneva_test.SLDASM
111.2 x 72.0 x 621.0 mm
tray_backward_top_slider
geneva_shaft
nema 17
geneva_slider2

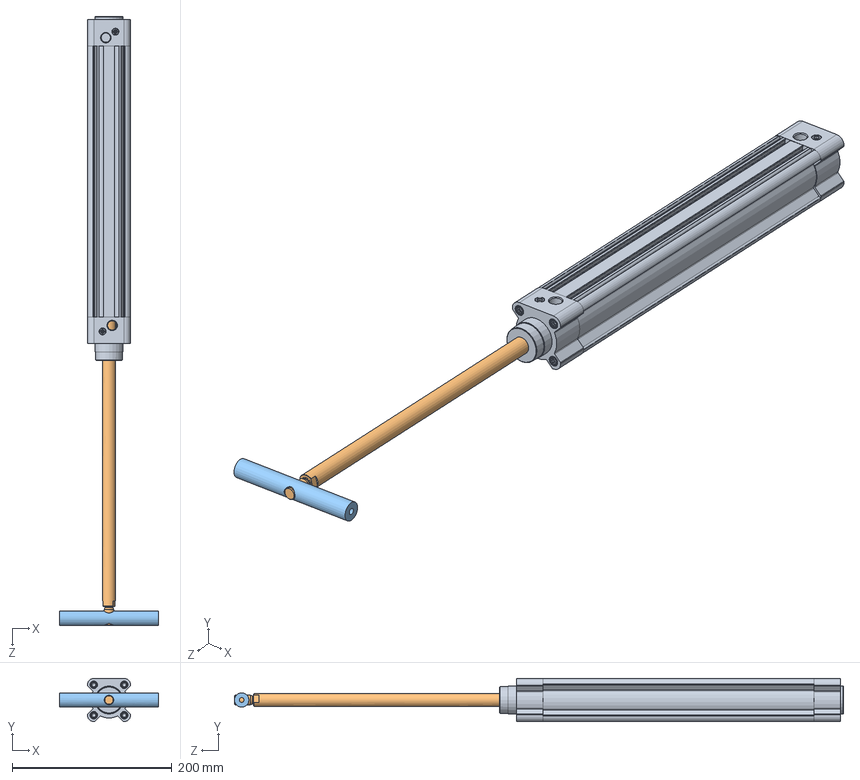
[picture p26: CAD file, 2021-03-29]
CAD Files/Development/Transplantation/planter/pneumatic_1/dsbc-40-300-ppva-n3.SLDASM
124.0 x 54.0 x 761.9 mm
dsbc-40-300-ppva-n3_01
dsbc-40-300-ppva-n3_02
connecting_rod_1

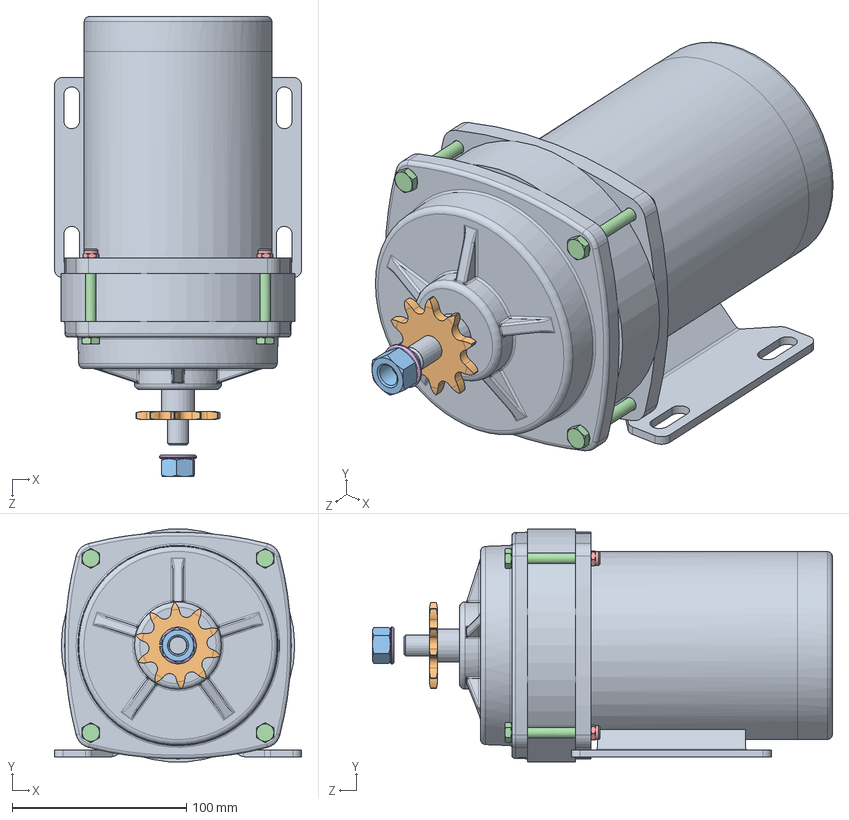
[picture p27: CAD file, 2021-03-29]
CAD Files/Development/Base/Motor/Throttle_motor/1020ZXF-36V_500W.SLDASM
142.0 x 133.6 x 263.9 mm
1020ZXF-36V_500W_Motor(Domyœlna_As Machined_)
Chain wheel DIN 8192 - A 10Z 083
ISO 4034 - M12
ISO 4017 - M6 x 50 x 4
ISO 10511-M5 x 4
DIN 128 - A12

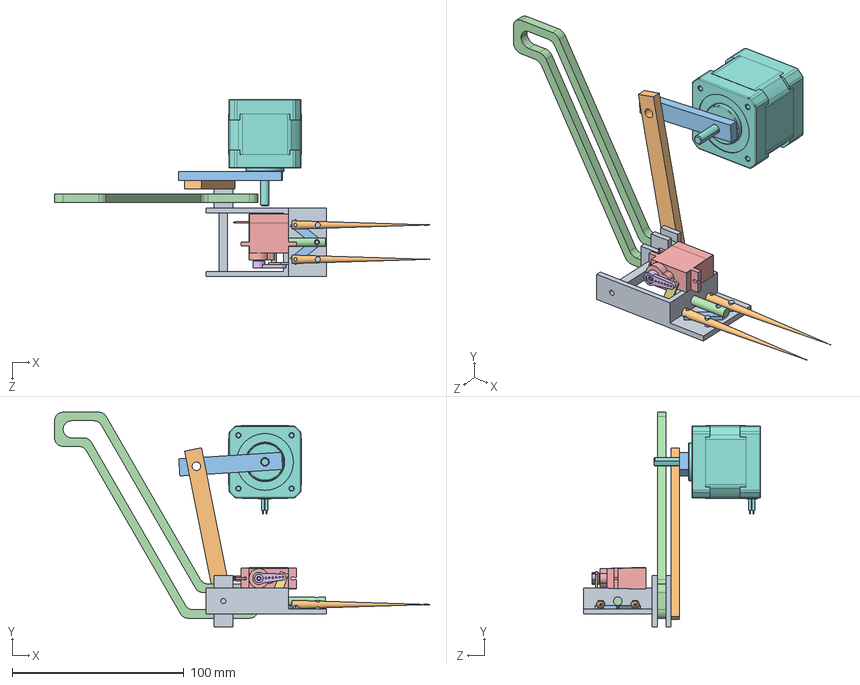
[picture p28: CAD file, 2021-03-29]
CAD Files/Development/Transplantation/seedling extractor/seedling gripper/gripper_asm.SLDASM
218.2 x 125.0 x 103.0 mm
gripper_arm_mount
gripper_arm x 2
rod1 x 2
rod2
Tower Pro 9g Micro Servo SG90
SG90 plastic Horn
linear_link
nema 17
guide_slider
path_link2
path_link1
travel_path

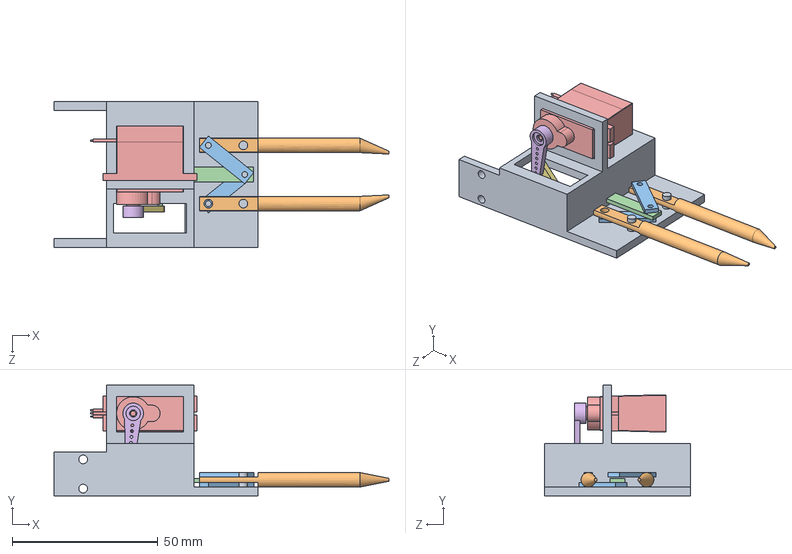
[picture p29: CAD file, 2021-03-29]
CAD Files/Development/Transplantation/seedling extractor/seedling gripper2/gripper.SLDASM
115.0 x 38.0 x 50.0 mm
gripper_base
gripper_arm x 2
gripper_arm_link x 2
gripper_crank
Tower Pro 9g Micro Servo SG90
SG90 plastic Horn
gripper_crank2

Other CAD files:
CAD Files/Development/Transplantation/seedling extractor/seedling gripper2/micro-servo-9g-sg90-tower-pro-1.snapshot.2/Tower Pro 9g Micro Servo SG90.SLDASM
CAD Files/Development/Base/movement_assem_R.SLDASM
CAD Files/Development/Transplantation/seedling extractor/seedling tray/v-slot-wheels-1.snapshot.1/v wheel.SLDASM
CAD Files/Development/Base/steering_assem.SLDASM
CAD Files/Development/Agitator/Agitator-Assembly.SLDASM
CAD Files/Development/Agitator/Agitator-Disk.SLDPRT
CAD Files/Development/Agitator/Agitator-Platform.SLDPRT
CAD Files/Development/Agitator/Pipe.SLDPRT
CAD Files/Development/Agitator/TG06-DCMotor.SLDPRT
CAD Files/Development/Base/Chassis/C-clamp.SLDPRT
CAD Files/Development/Base/Chassis/base_plate.SLDPRT
CAD Files/Development/Base/Chassis/base_rod.SLDPRT
CAD Files/Development/Base/Chassis/battery_box.SLDPRT
CAD Files/Development/Base/Chassis/battery_box_lid.SLDPRT
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
